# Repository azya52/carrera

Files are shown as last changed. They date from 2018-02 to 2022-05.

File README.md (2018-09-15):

# CarAttiny25
Custom firmware for Carrera Digital 143 decoder. All functions work with standart Digital 143 Black Box. 

Additional features:
- Ghost car funciton,
- Speed limit,
- Front light support.

I also plan to add support for the stop light.

# MiniCarreraDecoder
Reduced copy of the original decoder Carrera Digital 143.

**v4_SingleLayer** - is a single sided PCB, convenient for home production.

**v6** - a double sided variant, has a smaller size.

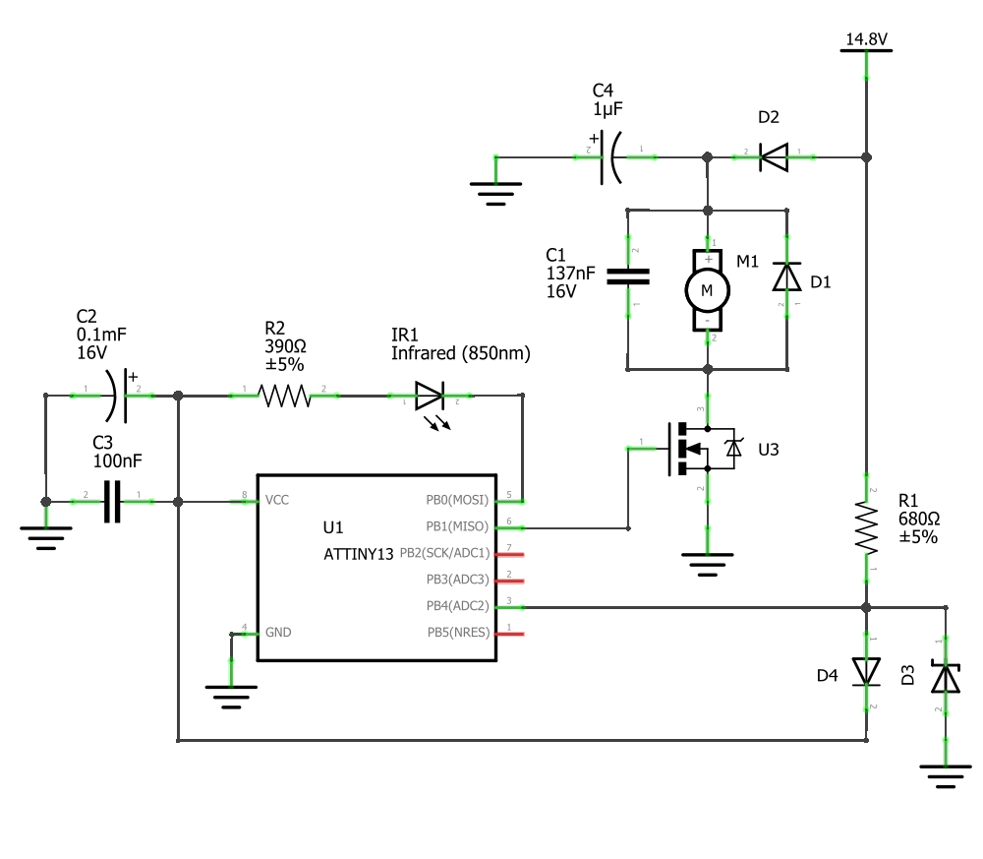
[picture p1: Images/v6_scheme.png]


* U1 - ATtiny25V-10SU (or ATtiny25-20SU)
* U3 - IRLML2030TRPBF
* R1 - 0603 680Ω
* R2 - 0603 390Ω
* D1 - FDLL300A
* D2 - LL4148
* D3 - BZX384-C5V6.115
* D4 - BAS321.115
* C1 - 0603 100nF
* C2 - 0.1mF (electrolitic)
* C3 - 0603 100nF
* C4 - 1μF (tantalum)

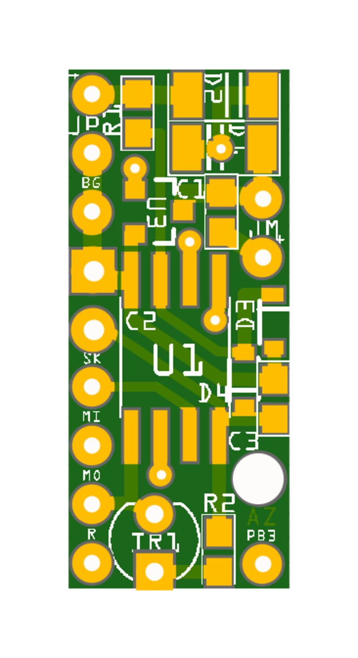
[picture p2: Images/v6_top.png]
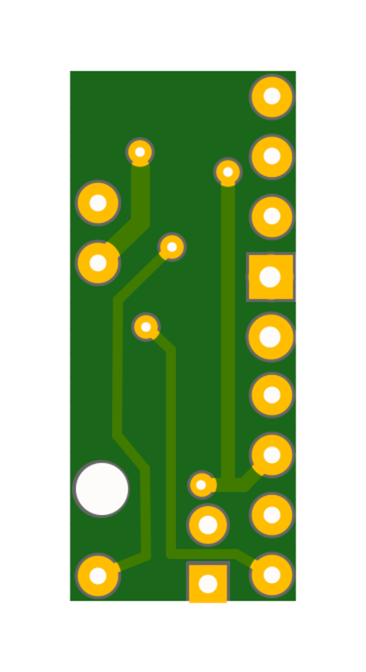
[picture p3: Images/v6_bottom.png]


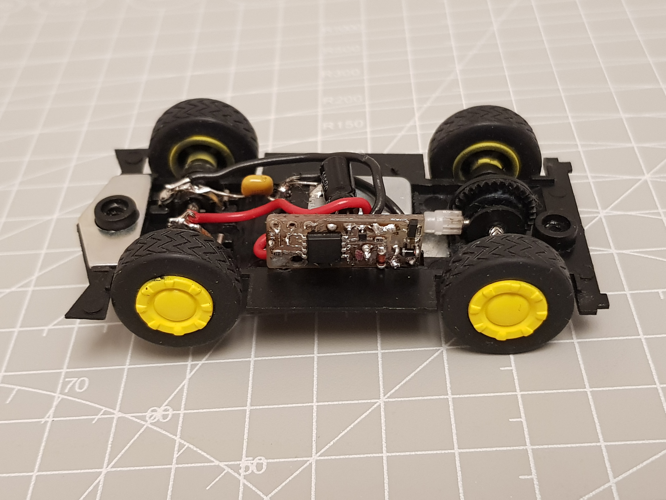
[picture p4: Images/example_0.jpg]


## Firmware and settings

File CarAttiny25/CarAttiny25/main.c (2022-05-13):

/*
 * CarAttiny25.c
 *
 * Created: 08.01.2018 15:27:24
 * Author : Alexander Zakharyan
 */ 

#include <avr/io.h>
#include <util/delay.h>
#include <avr/interrupt.h>
#include <avr/eeprom.h>
#include <avr/sleep.h>
#include <avr/power.h>

#define TRACK_PIN PB4
#define MOTOR_PIN PB1
#define IRLED_PIN PB0
#define FRONTLIGHT_PIN PB3
#define STOPLIGHT_PIN PB2
#define NU_PIN3 PB5

#define PACKET_PERIOD_MS 75
#define DBLCLICK_DELAY_MS 250
#define DBLCLICK_DELAY DBLCLICK_DELAY_MS/PACKET_PERIOD_MS
#define STOPBEFORELIGHT_DELAY_MS 3000
#define STOPBEFORELIGHT_DELAY STOPBEFORELIGHT_DELAY_MS/PACKET_PERIOD_MS
#define STOPLIGHT_DELAY_MS 500
#define STOPLIGHT_DELAY STOPLIGHT_DELAY_MS/PACKET_PERIOD_MS

#define TRANSM_FREQ 9800
#define PERIOD_QURT_CICLES F_CPU/TRANSM_FREQ/4

#define PROG_WORD_CHECK 12
#define ACTIV_WORD_CHECK 7
#define CONTROLLER_WORD_CHECK 9

#define GHOST_CAR_ID 6
#define PACE_CAR_ID 7

#define SHORT_TONE_MS 100
#define LONG_TONE_MS 200

#define MIN_CAR_SPEED_MULTIPLIER 9
#define MAX_CAR_SPEED_MULTIPLIER 14

uint8_t EEMEM eeprom_carID; 
uint8_t EEMEM eeprom_progInNextPowerOn; 
uint8_t EEMEM eeprom_ghostSpeed; 
uint8_t EEMEM eeprom_speedMultiplier; 
uint8_t EEMEM eeprom_lightOn;

uint8_t volatile carID = 255;
uint8_t volatile currentSpeed = 0;
uint8_t volatile sincWordIndex = 0;
uint8_t volatile doubleClickControllerId = 255;
uint8_t volatile countClickSW = 0;
uint8_t volatile notClickSWTime = 0;
uint8_t volatile progMode = 0;
uint8_t volatile progGhostMode = 0;
uint8_t volatile progSpeedMode = 0;
uint8_t volatile ghostSpeed = 0;
uint8_t volatile speedMultiplier = 14;
uint8_t volatile progSpeedSelecter = 0;
uint8_t volatile lightOn = 0;
uint8_t volatile stopTime = 0;
uint8_t volatile stopLightTime = 0;
uint8_t volatile lastSpeed = 0;

void playTone() {
	cli();
	TCCR0B = (0 << WGM02) | (1 << CS01) | (1 << CS00); // div 64
	OCR0B = 240;
	_delay_ms(150);	
	OCR0B = 255;
	TCCR0B = (0 << WGM02) | (1 << CS00); // no div
	sei();
}

void timersInit() {
	// MOTOR PWM
	TCCR0A = (1 << COM0B0) | (1 << COM0B1) | (3 << WGM00);
	TCCR0B = (0 << WGM02) | (1 << CS00); // no div
	OCR0B = 255;

	// LED PWM
	TCCR1 |= (1 << CTC1) | (1 << PWM1A) | (1 << COM1A0) | (1 << CS12) | (1 << CS10); // div 16
}

void startLEDPWM() {
	OCR1C = 32 * (carID + 1);
	OCR1A = OCR1C - 16;
}

void pinsInit() {
	DDRB = (1 << MOTOR_PIN) | (1 << IRLED_PIN) | (1 << FRONTLIGHT_PIN) | (1 << STOPLIGHT_PIN); //sets as output
	
	PORTB = (1 << TRACK_PIN); //PullUp TRACK
	PORTB |= (1 << NU_PIN3); //PullUp not used pins
}

void interruptsInit() {
	GIMSK = (1 << PCIE); //turn on PCINT
	MCUCR = (1 << ISC01) | (0 << ISC00); // falling front
	PCMSK = (1 << TRACK_PIN); //turn on interrupts only on TRACK
	sei();
}

void setCarSpeed(uint8_t speed) {
	currentSpeed = speed;
	OCR0B = 255 - speed * speedMultiplier;	
}

void setCarID(uint8_t newId) {
	carID = newId;
	eeprom_write_byte(&eeprom_carID, newId);
	startLEDPWM();
}

void calcStopTime(uint8_t speed) {
	if (speed == 0) {
		if (stopTime < 255) {
			stopTime++;
		}
	} else {
		stopTime = 0;
	}
}

void setLights() {
	PORTB &= ~((1 << FRONTLIGHT_PIN) | (1 << STOPLIGHT_PIN));
	PORTB |= (lightOn & ((1 << FRONTLIGHT_PIN) | (1 << STOPLIGHT_PIN)));
}

void blinkLights() {
	PORTB ^= (1 << FRONTLIGHT_PIN);	
}

void switchFrontLight() {
	stopTime = STOPBEFORELIGHT_DELAY - DBLCLICK_DELAY;
	lightOn = ~lightOn;
	eeprom_write_byte(&eeprom_lightOn, lightOn);
	setLights();
}

void calcStopLightTime(uint8_t speed) {
	if (lastSpeed - speed > 2) {
		stopLightTime = STOPLIGHT_DELAY;
		setLights();
	} else {
		if (stopLightTime > 0) {
			stopLightTime--;
		}
	}
}

void stopLightMiddleOn() {
	if (lightOn && (stopLightTime == 0)) {
		PORTB ^= (1 << STOPLIGHT_PIN);
	}
}

void stopProg() {
	if (progSpeedMode) {
		speedMultiplier = MIN_CAR_SPEED_MULTIPLIER + progSpeedSelecter;
		progSpeedMode = 0;
		eeprom_write_byte(&eeprom_speedMultiplier, speedMultiplier);	
	}
	progMode = 0;
}

void onMultiClick(uint8_t controllerId, uint8_t clickCount) {
	if (progGhostMode) {
		ghostSpeed = currentSpeed;
		currentSpeed = 0;
		progGhostMode = 0;
		progMode = 0;
		eeprom_write_byte(&eeprom_ghostSpeed, ghostSpeed);
		setCarID(GHOST_CAR_ID);
		playTone();
	} else if (progSpeedMode) {
		playTone();
		progSpeedSelecter++;
		if (progSpeedSelecter == 5) {
			_delay_ms(50);
			playTone();
			stopProg();
		}
	} else if ((clickCount > 1) && (currentSpeed == 0)) {
		playTone();
		if (progMode) {
			_delay_ms(50);
			playTone();
			if (clickCount == 2) {
				setCarID(controllerId);
			} else if (clickCount == 3) {
				progSpeedMode = 1;
				progSpeedSelecter = 0;
			} else if (clickCount == 4) {
				carID = controllerId;
				progGhostMode = 1;
			} else {
				progMode = 0;
			}
		} else {
			eeprom_write_byte(&eeprom_progInNextPowerOn, 1);
		}
	}
}

void checkDblClick(uint8_t controllerId, uint8_t sw) {
	if (sw) { //not pressed
		if (controllerId == doubleClickControllerId) {
			if (notClickSWTime == 0) {
				countClickSW++;
			}
			if (notClickSWTime++ > DBLCLICK_DELAY) {
				doubleClickControllerId = 255;
				if (countClickSW > 0) {
					onMultiClick(controllerId, countClickSW);
				}
			}
		}
	} else {
		if (controllerId < doubleClickControllerId) {
			doubleClickControllerId = controllerId;
			countClickSW = 0;
		}
		if (doubleClickControllerId == controllerId) {
			notClickSWTime = 0;
		}
	}
}

void onProgramDataWordReceived(uint16_t word) {

}

void onActiveControllerWordReceived(uint16_t word) {
	uint8_t parity = word & 0xFE;
	parity = parity ^ (parity >> 4);
	parity ^= parity >> 2;
	parity ^= parity >> 1;
	parity &= 0x01;
	if (parity == (word & 0x01)) {
		return;
	}
	
	uint8_t anyKeyPressed = word & 0x7F;
	if (anyKeyPressed) {
		stopProg();
	}
	
	uint8_t currentKeyPressed = (word << (carID & 0x0F)) & 0x40;
	if (carID == GHOST_CAR_ID) {
		if ((currentSpeed == 0) && anyKeyPressed) {
			setCarSpeed(ghostSpeed);
		}
	} else {
		if (currentKeyPressed) {
			if (currentSpeed == 0) {
				setCarSpeed(1);
			}
		} else {
			setCarSpeed(0);
		}
	}
}

void onControllerWordReceived(uint16_t word) {
	uint8_t controllerId = (word >> 6) & 0x07;
	uint8_t speed = (word >> 1) & 0x0F;
	uint8_t sw = (word >> 5) & 1;
	if (controllerId == carID) {
		setCarSpeed(speed);
		calcStopTime(speed);
		calcStopLightTime(speed);
		if (!sw && (stopTime > STOPBEFORELIGHT_DELAY) && !progMode) {
			switchFrontLight();
		}
		lastSpeed = speed;
	} 
	checkDblClick(controllerId, sw);
}

void onWordReceived(uint16_t word) {
	stopLightMiddleOn();
	if ((word >> CONTROLLER_WORD_CHECK) == 1) {
		if ((word >> 6) != 0x0F) {
			onControllerWordReceived(word);
		}
	} else
	if ((word >> PROG_WORD_CHECK) == 1) {
		onProgramDataWordReceived(word);
	} else
	if ((word >> ACTIV_WORD_CHECK) == 1) {
		onActiveControllerWordReceived(word);
	}
}

ISR(PCINT0_vect) {
	uint8_t start = TCNT0;
	while ((uint8_t) (TCNT0 - start) < PERIOD_QURT_CICLES);
	start += PERIOD_QURT_CICLES;
	uint8_t firstHalfCycle = 1;
	uint8_t secondHalfCycle = 0;
	uint16_t receivedValue = 0;
	while (firstHalfCycle != secondHalfCycle) {
		receivedValue = (receivedValue << 1) | firstHalfCycle;

		while ((uint8_t) (TCNT0 - start) < PERIOD_QURT_CICLES);
		start += PERIOD_QURT_CICLES;
		while ((uint8_t) (TCNT0 - start) < PERIOD_QURT_CICLES);
		start += PERIOD_QURT_CICLES;

		firstHalfCycle = (PINB >> TRACK_PIN) & 1;

		while ((uint8_t) (TCNT0 - start) < PERIOD_QURT_CICLES);
		start += PERIOD_QURT_CICLES;
		while ((uint8_t) (TCNT0 - start) < PERIOD_QURT_CICLES);
		start += PERIOD_QURT_CICLES;
		
		secondHalfCycle = (PINB >> TRACK_PIN) & 1;
	}
	onWordReceived(receivedValue);
	GIFR = 1 << PCIF;
}


int main(void) {
	carID = eeprom_read_byte(&eeprom_carID);
	ghostSpeed = eeprom_read_byte(&eeprom_ghostSpeed);
	speedMultiplier = eeprom_read_byte(&eeprom_speedMultiplier);
	if (speedMultiplier > MAX_CAR_SPEED_MULTIPLIER) {
		speedMultiplier = MAX_CAR_SPEED_MULTIPLIER;
	}
	progMode = eeprom_read_byte(&eeprom_progInNextPowerOn);
	if (progMode) {
		if (progMode > 1) {
			progMode = 0;
		}
		eeprom_write_byte(&eeprom_progInNextPowerOn, 0);	
	}
	lightOn = eeprom_read_byte(&eeprom_lightOn);
	
	power_adc_disable();
	power_usi_disable();
	//ADCSRA = 0; //disable the ADC

	pinsInit();
	timersInit();
	startLEDPWM();
	setLights();
	interruptsInit();
	
	set_sleep_mode(SLEEP_MODE_IDLE);
	while (1) {
		sleep_enable(); 
		sleep_cpu(); 
	}
}

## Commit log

2018-01-22 improved stability
    add sleep
    change receive checker
    change speed select logic
    [main.c]
2018-02-02 Add Decoder gerber
    [CarMyPrefBoardSMDv4_contour.gm1, CarMyPrefBoardSMDv4_copperBottom.gbl, CarMyPrefBoardSMDv4_copperTop.gtl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]
2018-02-02 add pcb images
